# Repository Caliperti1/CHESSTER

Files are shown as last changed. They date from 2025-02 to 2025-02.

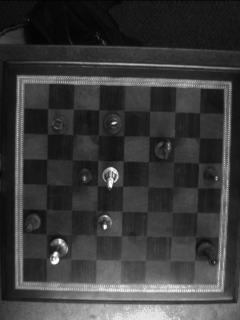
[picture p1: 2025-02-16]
MATLAB/Demo Moved.bmp

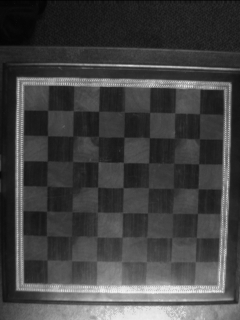
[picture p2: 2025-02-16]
MATLAB/Demo Blank.bmp

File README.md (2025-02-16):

# CHESSTER
Cerebral Harnessing Education Sidekick for STrategic Engineering Research (Chess Robot for Teaching Computer Aided Engineering)

I originally built this project after teaching enginering design, computer aided deisgn, and computational analysis and realzing that students struggled to see how these skills connect to build a cohesive engineering project. 

After using this in class a few students asked to start doing an indepedent study to look into ways of improving the ssytem. Subsequent updates to this repo will be the result of their work!

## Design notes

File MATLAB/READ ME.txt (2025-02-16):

Desktop Chess 
Version 0.1 
Chris Aliperti 
United States Military Academy Department of Civil and Mechanical Engineering 
28 October 2023

--------------------------------------------------------------------------------
Project Overview:

--------------------------------------------------------------------------------
Version Notes:

--------------------------------------------------------------------------------
Arduino Camera:
	This version uses an OV7670 and an arduino on a rig to capture images at 
	every 3 seconds and store them in a folder. 
	Tutorial: https://www.instructables.com/OV7670-Arduino-Camera-Sensor-Module-Framecapture-T/

--------------------------------------------------------------------------------
Solidworks:
	Soldiworks assembly shows camera rig using arduino Uno, OV7670 and 1020 alluminum 

--------------------------------------------------------------------------------
Matlab Functions 

	* denotes unused or archived functions 

	greyScale - normalizes an image to greyscale values (0-1)
		input: image (mxnx3)
		output: normalized image (mxn)

	*BW - turns image to black an dwhite, using mean pixel value as 	threshhold 
		input: image (mxnx3)
		output: BW image with vlaues of 0 or 255 (mxnx3) 

	*squareOffRig - trims image to square matrix with only board using set dimensions based off the camera rig. Archived due to inability to adapt to slight sifts in board or rig.
		input - image (mxnx3)
		output - sqaure image martix where deimasion a is based off difference between provided upper,lower,left adn right ounds of board (axax3) 

	sobelMask - finds edges within an image using a 3x3 mask convoluted over image. Gradient of convolution matrix is calculated and value is compared to a threshold and pulled to rail based on thrshold criteria.
	input - image (nxmx3)
		thresh - value between 0 and 1. hgiher number will make filter more selective 
	output - image of edges (nxm)

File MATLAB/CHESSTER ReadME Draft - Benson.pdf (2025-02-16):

CHESSTER README word doc
play
BLUF: The play function encompasses all of the functions that enable CHESSTER to play with its human opponents through computer vision and an exchange of information between MatLab and Arduino.
- Establishes variables for connection to Arduino serial port. (sets baud rate, loads default camera positions from given files).
- Prompts user in MatLab to recalibrate camera over the chess board
- Reads response and calls calibrateCamera function with the default camera positions as inputs or displays blank image.
- Calls startGame function and sets turn to 0
- Establishes serial connection to Arduino and waits at most 10 minutes before moving to next turn.
- While turn is 0, MatLab communicates to Arduino and displays a standby message. Arduino receives the communication and calls the startPlay function, which changes the standby message on the LCD to a read to play message and send a ready signal back to MatLab.
- MatLab receives start signal and calls the captureImage function, which sets the default image of the chess board, and displays its own ready message while also advancing the turn.
- Arduino receives ready signal from MatLab and prompts the user to begin their move, as well as to press the button on the LCD after their move.
- When the button is pressed, Arduino runs the signalMove function which displays a loading message on the LCD screen and sends a play signal to MatLab.
- When MatLab receives the play signal, it causes the camera to take another image of the board with captureImage, then it runs computer vision by calling the camPassForward function which takes the original image of the board, new image of the board, and startGame functions to run. MatLab then runs the engine for Chesster using the engPassForward function. Moves made are translated and sent to Arduino using json and sent to Arduino.
- Move is received by Arduino, and displays a confirmation message on the LCD, while communicating with MatLab as well.
- Arduino makes a decision based on kill values sent with the move data and displays that the move was received and whether a piece was taken with its move, finally displaying a move complete message (sending another message to MatLab) and prompting the user to make another move and advancing the turn, otherwise an error message will display.
- As MatLab receives confirmation, it displays the acknowledgement and the move made using the showOff function, as well as advancing the turn. When the move complete message is received, MatLab runs the updateGame function and takes another picture of the board using the captureImage function.
- As the player makes another move, the process repeats itself.
Computer Vision

captureImage
BLUF: The captureImage starts the camera and saves images taken to the landing directory, as well as identifying the image for use by other functions later.
Inputs: camDir, landingDir, camKIllBatDir (Directories for starting and stopping the camera, as well as storing the images.
Outputs: Images
- Runs the initiateCamera function with the camera directory as the input.
- Identifies the open directory folder as the original directory, then sets a stat variable as 1.
- While loop that runs when stat = 1, changes open folder to the landing directory folder (where pictures go), sets a search variable “a” to identify any objects in the directory with a .bmp file identifier. Sets variable “n” as the number of objects identified by the “a” variable.
- If statement, that initiates when the number of objects in the landing directory is greater than 9, which in turn runs the kill function to stop the camera from taking photos. If successful, then a script will print stating it executed the kill, otherwise it will display an error message.
- Stat is set to 0, ending the while loop.
- Switches open folder to the landing directory in case it is not, sets the image to the 6th image taken (higher resolution)
- Removes images that it did not identify in the previous step from the landing directory.
- Sets open folder back to the original directory.
initiateCamera
BLUF: Starts camera
Inputs: camDir (Directory that contains the command to start the camera) Outputs: Camera starts
- Sets open folder as the original directory.
- Try (Executes code)
- Sets open folder as the input directory from captureImage.
- Sets the command variable to the code that starts the camera
- Tells Command Prompt to run the start command.
- Sets open folder to the original directory
- Displays a message when command is sent.
- Catch (Catches errors)
- Sets open folder to the original directory
- Displays error message.
calibrateCamera
BLUF: Captures image of blank board and ensures camera is working properly.
Inputs: camDir, landingDir, camKIllBatDir (Directories for starting and stopping the camera, as well as storing the images.
Outputs: Calibrated image of the blank board

- Sets confirmation variable to a default, while default user will be prompted to “press any button when ready to calibrate”
- When a button is pressed, and the ready variable is changed, an if statement is executed, setting the blank image as a variable, that uses the output of the captureImage function.
- squareOffTestFig function is executed with the blank image as the input
- User is prompted to press “Y” to confirm calibration or “N” if a new image needs to be taken. This input replaces the previous confirmation variable.
- A full file specification using the landing directory folder and the 6.bmp image from the folder is set to a current image name variable.
- A second if statement is executed if the user answers the calibration prompt with “Y”.
- A blank.bmp filename is created for the landing directory folder and set as the new image name variable.
- The current image name is changed to the new image name “blank.bmp”
- The blank image variable is reset to the blank.bmp image, and a message is sent confirming the name change.
- All files excluding the newly named .bmp are cleared from the landing directory folder.
squareOffTestFig
BLUF: Takes blank board image, squares it off and makes it greyscale.
Inputs: Initial image of the blank board
Outputs: Calibrated image of the blank board
- Calls sobelMask function, with the blank board image as an input and with a very high threshold in order to outline the entirety of the board.
- Calls the squareOff function with the blank board as the input and isolates the board.
- Displays the three new images in a figure for the user to see.
sobelMask
BLUF: Finds edges and generates an edge map image of the board and squares within. Inputs: Initial blank image of the board, color threshold fo identifying pixels as black or white.
Outputs: Image of the identified white areas on the board.
- Calls greyScale function in input image, normalizing color values between 0 and 1
- Defines the “Mask” matrix to be used in the Sobel.
- Convolutes the mask matrix over the image matrix and returns a convolution matrix, then calculates the magnitude of the convolutions.
- Stores the magnitudes as 1-bit integers as the output of the function.
greyScale
BLUF: Normalizes an image (0 - white, 1 – black) *Figure out numbers in function

Inputs: Initial blank image of the board
Outputs: Grayscale image of the blank board.
- The input image’s colors are reassigned as either black or white depending on which they are closer to in color, and assigned to the output variable. squareOff
BLUF: Square off input image and isolate Board based on calculated bounds.
Inputs: Initial blank image of the board
Outputs: Image of the board after identifying and applying the boundaries of the board in the image.
- Sets the bounds to a variable bound that calls the boardBounds function using the input image to the squareOff function as the same input.
- Sets the x and y bounds of the new squared image as the bounds found in the boards function.
boardBounds
BLUF: ID edges of the board, starting at the center of the sobelmasked image and finds the coordinate of the first edge in each direction with a high threshold, then trims the image to be square.
Inputs: Initial blank image of the board
Outputs: Greyscale image of the board with boundaries applied after identification through use of the Sobel mask.
- Calls the sobelMask function, with the input image and a high threshold.
- Determines the size of the sobelmasked image, then finds the center of it.
- Initiates four while loops that move in each direction until an edge is found
- Coordinates of the edges are put in to a matrix as the output. camPassForward
BLUF: Passes forward the updated game matrix to the engine, using the blank board image, the board image before the move, an image of the board after the move, and a matrix that represents the original image as inputs.
Inputs: Calibrated image of the blank board, an image of the set board before a move, an image of the set board after a move, and the game matrix that represents the board state before a move. Outputs: Updated game matrix that represents the board after a move.
- Calls the findMove function to calculate what on the board has changed.
- Calls the updateGame function to update the game matrix.
findMove
BLUF: Takes blank image of board, the image of the board before the move, and the image of the board after the move and determines what move was made. *Change variables around, check functionality.

Inputs: Calibrated image of the blank board, an image of the board before a move, and an image of the board after a move.
Outputs: Coordinates of the piece before and after it has moved.
- Calls the moveLoc function to find the starting location of the piece and the ending location of the piece, then assigns them to a matrix as the output.
moveLoc
BLUF: Analyzes the input images of the original board and the board with the move made, and determines what move occurred.
Inputs: Calibrated image of the blank board, an image of the board before a move, and an image of the board after a move.
Outputs: Coordinates of the piece being moved in both images and an associated confidence.
- Finds the area in the images where the numerical values in the matrixes differ
- The difference is run through the sobelMask function
- The sobelmasked image is run through the squareOff2 function using the blank board bounds.
- The square bounds of the blank board are then found using the squareOff function, and the sqaureBounds function, which is then assigned as an 8x8 matrix.
- A score is then calculated that gauges the confidence of the move detected by the series of functions.
squareOff2
BLUF: Square off image and isolate Board based on calculated bounds from a blank board
Inputs: Initial blank image of the board, and the Sobel mask of the difference between the images of the board before and after a move.
Outputs: Image of the board after identifying and applying the boundaries of the board in the image.
- Sets the bounds to a variable bound that calls the boardBounds function using the input image to the squareOff function as the same input.
- Sets the x and y bounds of the new squared image as the bounds found in the boardBounds function.
sqaureBounds
BLUF: Creates bounds for the squared image input.
Inputs: Squared image of the blank board
Outputs: Bounds for each square on the chess board.
- Creates dimensional increments of 8 from left to right and top to bottom.
- Creates vectors of these bounds, then corrects them.
- Creates an array that stores the squares in the vicinity of each other.

showOff
BLUF: Plots images of the board before the move and after the move, as well as the results of the computer vision stage.
Inputs: Calibrated image of the blank board, an image of the set board before a move, an image of the set board after a move, and the game matrix that represents the board state before a move. Outputs: Figure that shows side by side images of the board before and after a move, and a digital version of the change the computer vision recognized on the board.
- Calls the findMove function with images of the blank board, board before the move and the board after the move as inputs.
- Assigns the pieces on the board coordinates for both the original board and the moved board using the mapToChess function.
- Calls the updateGame function using the game matrix and the move found.
- Displays a plot of the original board before the move and another of the board after the move, as well as the original and new game matrixes.
mapToChess
BLUF: Converts the matrix coordinates of the board to chess locations.
Inputs: Coordinates of the piece moved in the game matrix
Outputs: Location of the piece on the chess board in corresponding terms
- Assigns the matrix coordinates a chess board position (i.e. knight to a4) displayBoard
BLUF: Creates a figure of the digital representation of the current board give the game matrix. *Does not use the output in the function*
Inputs: The game matrix
Outputs: Figure that represents the current state of the board
- Calls the checkerBoard function and assigns it to a variable.
- Creates a vector of 8 evenly spaced points from 1 to 64 and an 8x8x2 position matrix of zeros.
- Assigns positions to four quadrants of the chess board individually, then compiles them into an image.
checkerBoard
BLUF: Creates a blank checkerboard pattern for plotting.
Inputs: None
Outputs: Blank checkerboard patter to be used to plot a digital representation of the chess board.
- Creates a matrix of ones to represent white, and a matrix of zeros to represent black, and assigns them to an overall matrix for the output.

updateGame
BLUF: Updates the game matrix based on the move made.
Inputs: The current game matrix and the coordinates of a piece before and after a move. Outputs: Updated game matrix for the board after a move has been made.
- Assigns the original position of the piece to x and y variables as well as the new location of the piece.
- Uses the position of the piece and identifies both its type and color using the game matrix as the reference.
- Overwrites the original position of the piece in the game matrix, and sets the new location of the piece in the game matrix.
startGame
BLUF: Creates the game matrix, with pieces at starting locations identified by both color and type. Inputs: None
Outputs: Original game matrix of a set board before any move has been made.
- Assigns a color and piece matrix for the starting board state.
Engine
engPassForward
BLUF: Generates a recommended move and translates it to steps for the motor using the game matrix and turn number as inputs and outputting piece and move locations, as well as info on whether a piece has been taken.
Inputs: Current game matrix and the current turn number.
Outputs: Positions of a piece before and after a move as well as information regarding whether a piece is taken.
- Calls the engine function with the game matrix and turn number as inputs.
- Takes the recommended move and separates it into the coordinates of the piece before and after the move.
- Size parameters are then set for the engine, in reference to the board as well as for the motor’s rotation.
- Sets kill conditions for when one player’s piece overtakes another.
engine
BLUF: Takes in the game matrix and turn, puts them through several layers of a decision tree, returning an array with the information for a recommended move.
Inputs: Current game matrix and the current turn number.

Outputs: A cell array with all relevant information for a recommended move.
- Creates the first layer of the decision tree using the firstLayer function, and a second using the secondLayer function with the first layer as an input.
- Creates a weighted move matrix using the firstLayerOutputWeighted with both layers.
- Attributes a score to the weighted matrix and creates a set of recommended moves. firstLayer
BLUF: Uses the game matrix and turn as inputs, outputting an 8x8 array, where each cell contains the moves the piece in that position can perform. *Nested 8x8 in each part of the output array.*
Inputs: Current game matrix and the current turn number.
Outputs: Cell array with all available moves for the pieces on the board.
- Determines the color of the piece based on the current turn.
- Calls the initFirstLayer function to create an empty move matrix as a shell for the first layer.
- Populates the first layer by running a for loop through the entire game matrix, and assigning moves from the pawnMoves, rookMoves, bishopMoves, knightMoves, queenMoves, and kingMoves based on the piece in each cell.
initFirstLayer
BLUF: Creates the first layer for the engine.
Inputs: None
Outputs: Empty cell array for use in the firstLayer function.
- Assigns the initialization as an 8x8 cell array
- Sets the values of the array as zeros.
secondLayer
BLUF: Creates the second layer of the decision tree for the engine, using the game matrix, turn, and the first layer as inputs.
Inputs: Current game matrix, the current turn number, and the first layer cell array. Outputs: Cell array of all possible moves for the user to make in response to any move possible to CHESSTER in the first layer.
- Determines the color of the piece based on the current turn.
- Calls the movedGame function with the first layer and the game matrix as inputs in order to create an input layer of all possible moved games that can occur as a result of the first layer.
- Calls the initSecondLayer function to create an empty move matrix as a shell for the second layer.
- Populates the second layer by running a for loop through the entire game matrix, and assigning moves from the pawnMoves, rookMoves, bishopMoves, knightMoves, queenMoves, and kingMoves based on the piece in each cell.

movedGame
BLUF: Creates a cell array of all moved games that can occur as a result of first layer moves to be used as inputs for the second layer, uses the first layer and the game matrix as inputs.
Inputs: Current game matrix and the first layer cell array.
Outputs: Cell array of all moved games that can occur as a result of first layer moves.
- Creates an empty cell array and populates it with data from the game matrix and first layer, showing all possible game movements from the game matrix to the first layer.
initSecondLayer
BLUF: Initializes the second layer for the engine using the output from the movedGame function as its input.
Inputs: movedGame cell array
Outputs: An empty input layer cell array.
- Assigns the initialization as an 8x8 cell array
- Sets the values of the array as zeros.
pawnMoves
BLUF: Uses the game matrix, and the position of the piece in the matrix, as inputs to create an 8x8 showing possible moves for pawns.
Inputs: Current game matrix and the coordinates of pawns in the given cell array. Outputs: Coordinates in the cell array of where each pawn could move legally on the board.
- Checks the color of the piece.
- Creates an 8x8 blank matrix for possible moves.
- Assigns if statements for the conditions of the board, to calculate what legal moves can be made for a pawn.
rookMoves
BLUF: Uses the game matrix, and the position of the piece in the matrix, as inputs to create an 8x8 showing possible moves for rooks.
Inputs: Current game matrix and the coordinates of rooks in the given cell array. Outputs: Coordinates in the cell array of where each rook could move legally on the board.
- Checks the color of the piece.
- Creates an 8x8 blank matrix for possible moves.

- Assigns if statements for the conditions of the board, to calculate what legal moves can be made for a rook.
bishopMoves
BLUF: Uses the game matrix, and the position of the piece in the matrix, as inputs to create an 8x8 showing possible moves for bishops.
Inputs: Current game matrix and the coordinates of bishops in the given cell array. Outputs: Coordinates in the cell array of where each bishop could move legally on the board.
- Checks the color of the piece.
- Creates an 8x8 blank matrix for possible moves.
- Assigns if statements for the conditions of the board, to calculate what legal moves can be made for a bishop.
knightMoves
BLUF: Uses the game matrix, and the position of the piece in the matrix, as inputs to create an 8x8 showing possible moves for knights.
Inputs: Current game matrix and the coordinates of knights in the given cell array. Outputs: Coordinates in the cell array of where each knight could move legally on the board.
- Checks the color of the piece.
- Creates an 8x8 blank matrix for possible moves.
- Assigns if statements for the conditions of the board, to calculate what legal moves can be made for a knight.
queenMoves
BLUF: Uses the game matrix, and the position of the piece in the matrix, as inputs to create an 8x8 showing possible moves for queens.
Inputs: Current game matrix and the coordinates of queens in the given cell array. Outputs: Coordinates in the cell array of where each queen could move legally on the board.
- Checks the color of the piece.
- Creates an 8x8 blank matrix for possible moves.
- Assigns if statements for the conditions of the board, to calculate what legal moves can be made for a queen.
kingMoves
BLUF: Uses the game matrix, and the position of the piece in the matrix, as inputs to create an 8x8 showing possible moves for kings.
Inputs: Current game matrix and the coordinates of kings in the given cell array.

Outputs: Coordinates in the cell array of where each king could move legally on the board.
- Checks the color of the piece.
- Creates an 8x8 blank matrix for possible moves.
- Assigns if statements for the conditions of the board, to calculate what legal moves can be made for a king.
firstLayerOutputWeighted
BLUF: Uses the game matrix, first layer, second layer, and turn number as inputs to weigh the decisions in the first and second layer, takes the difference, and applies the move to a “dictionary” where the overall maximum difference is chosen as the best move.
Inputs: Current game matrix, the first layer cell array, second layer cell array, and the current turn number.
Outputs: Score key associated with every possible move on the board.
- Determines the color of the piece based on the turn.
- Creates a weight dictionary for the value of each piece.
firstLayerOutput
BLUF: Checks the second layer and determines whether the move would result in the opponent being able to take CHESSTER’s king.
Inputs: Current game matrix, the first layer cell array, second layer cell array, and the current turn number.
Outputs: Weight of every move in the first layer cell array.
- Creates a cell array with all of the information about possible moves and their attributed score.
- Determines the location of the friendly king on the board.
- Creates an empty matrix the size of the second layer.
- Analyzes the moves available to CHESSTER using the listMoves function.
- Uses the second layer to determine which of the moves in the move list leave the opportunity for the user to take CHESSTER’s king.
- Determines if the move made by CHESSTER would be legal or would result in the loss of its king.
- Outputs a cell array with all relevant information pertaining to moves that could be made including piece identifying information, locations, scores related to moves, and the enemy’s best response.
listMoves
BLUF: Lists all moves available to CHESSTER from the first layer Inputs: Current game matrix and the first layer cell array. Outputs: List of all moves available from the first layer.
- Creates an empty string array

- Populates the array with information from the first layer, using the location from the first layer as it relates to the game matrix and calling the mapToChessPlot function to convert the game matrix coordinates to locations on the chess board.
mapToChessPlot
BLUF: Converts game matrix coordinates to chess locations. Inputs: Game matrix coordinates
Outputs: Corresponding chess board locations secondLayerOutput
BLUF: Translates the output of the second layer into a 7-cell array format. Inputs: Current game matrix and the second layer cell array.
Outputs: 7-cell array identifying each piece and its possible moves in response to the first layer
- For every possible move found in the second layer, it is assigned as part of the output array that identifies it by piece type, color, locations, score, and corresponding first layer move.

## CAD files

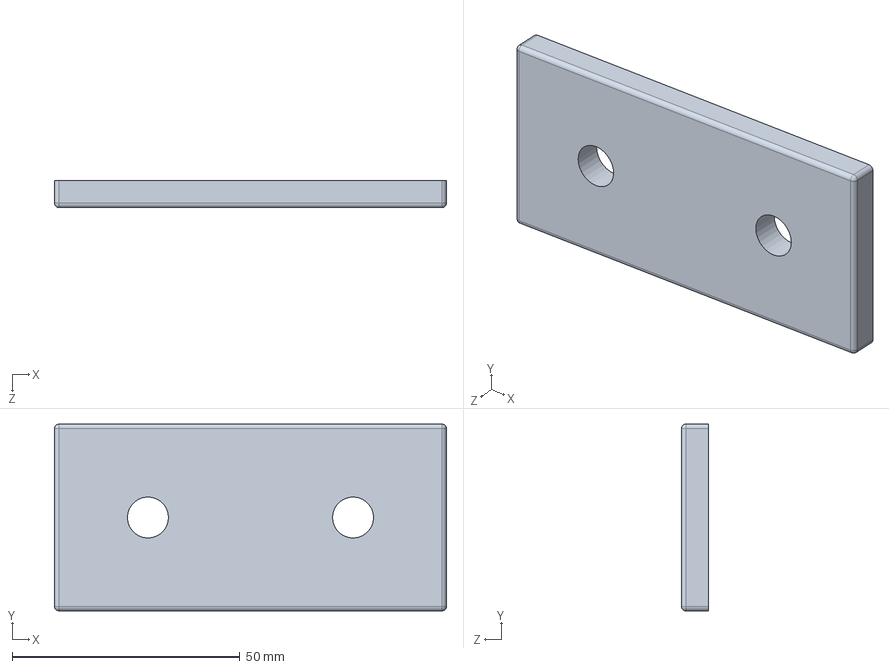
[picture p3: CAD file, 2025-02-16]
Solidworks/Straight connector.SLDPRT
86.0 x 41.0 x 6.00 mm

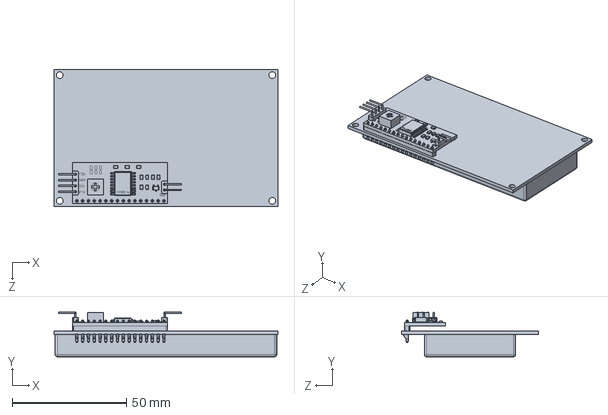
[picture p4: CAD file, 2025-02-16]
Solidworks/lcd 2004 i2c v1.SLDPRT
98.0 x 19.6 x 60.0 mm

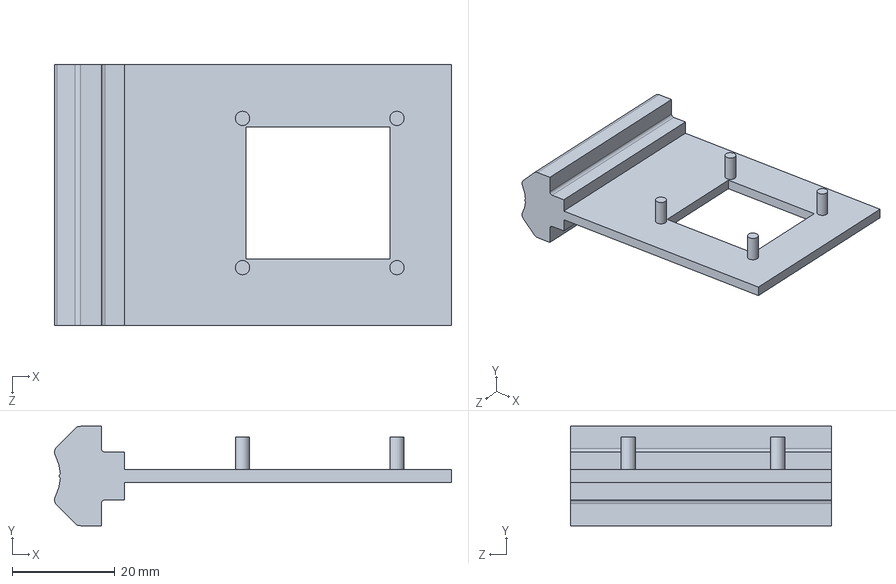
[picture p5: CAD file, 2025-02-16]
Solidworks/OV760 Camera Mount 10mm 8020.SLDPRT
77.1 x 19.3 x 50.8 mm

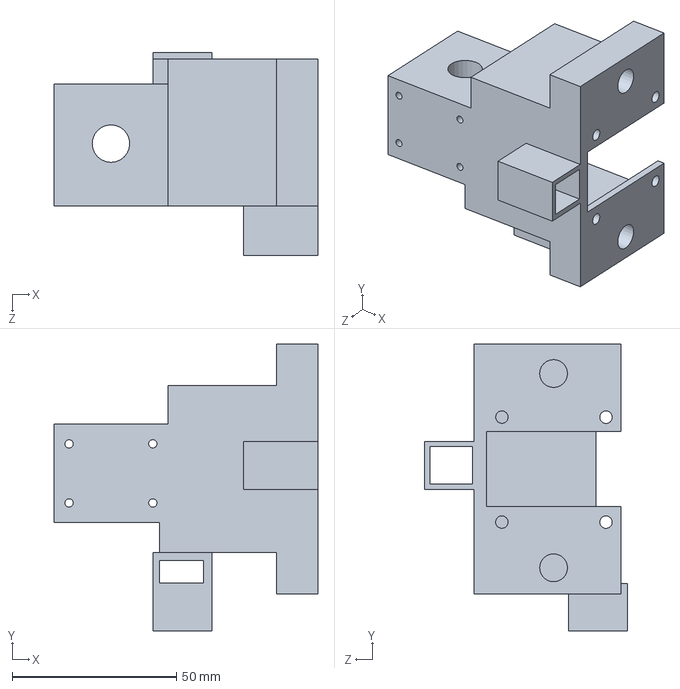
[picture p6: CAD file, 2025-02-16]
Solidworks/Motor Slider.SLDPRT
80.4 x 87.4 x 61.8 mm

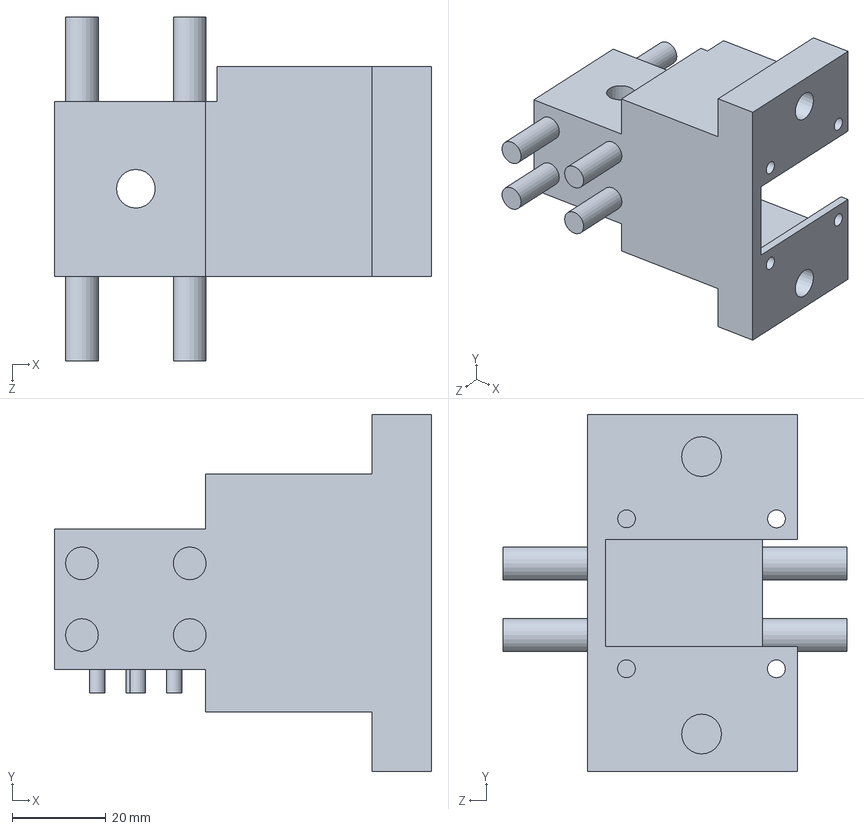
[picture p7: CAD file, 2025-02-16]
Solidworks/Motor Slider-DESKTOP-MGNFT40.SLDPRT
80.4 x 76.2 x 73.3 mm

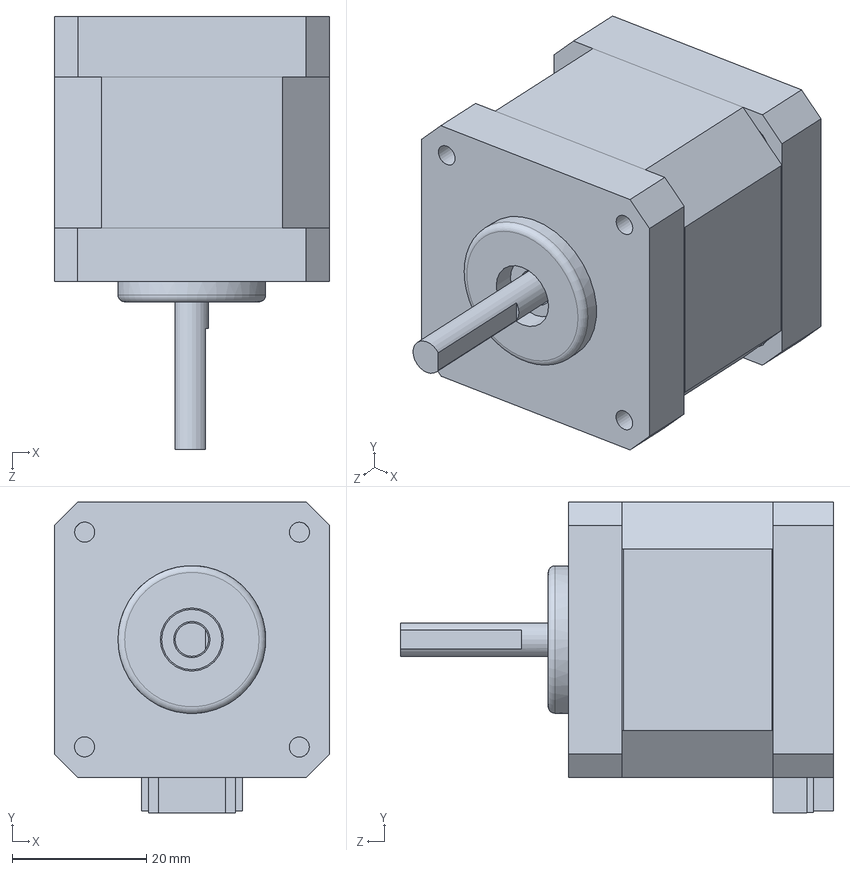
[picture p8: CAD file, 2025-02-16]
Solidworks/Nema 17 Stepper Motor v5.SLDPRT
41.0 x 46.3 x 64.5 mm

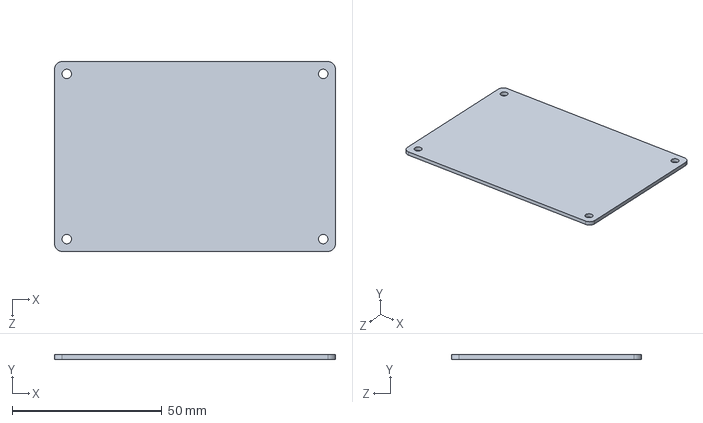
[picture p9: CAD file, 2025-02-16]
Solidworks/protoBoard.SLDPRT
94.0 x 1.52 x 63.5 mm

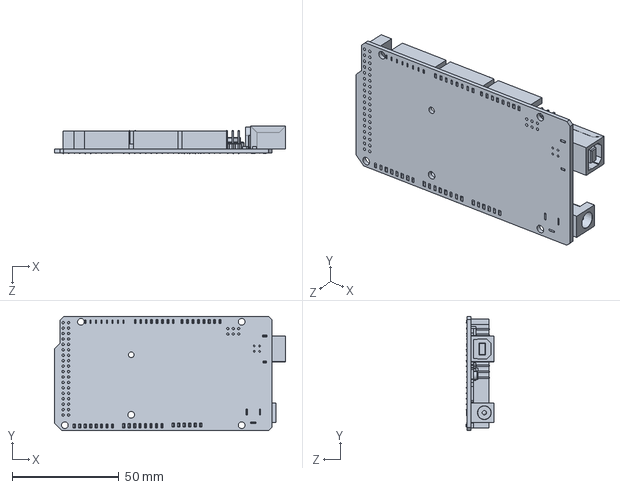
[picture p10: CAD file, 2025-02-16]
Solidworks/ArduinoMega.SLDPRT
107.9 x 53.4 x 13.0 mm

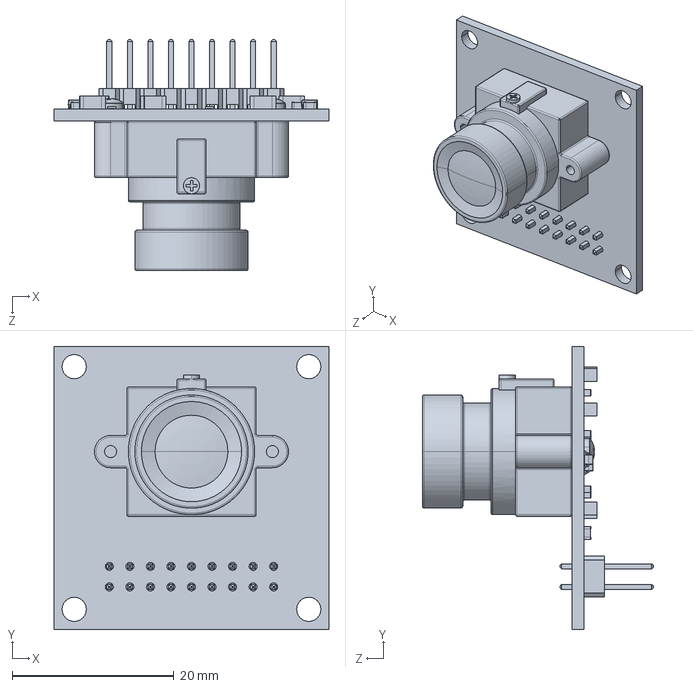
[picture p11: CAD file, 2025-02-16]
Solidworks/Camera OV7670.SLDPRT
34.0 x 35.0 x 28.6 mm

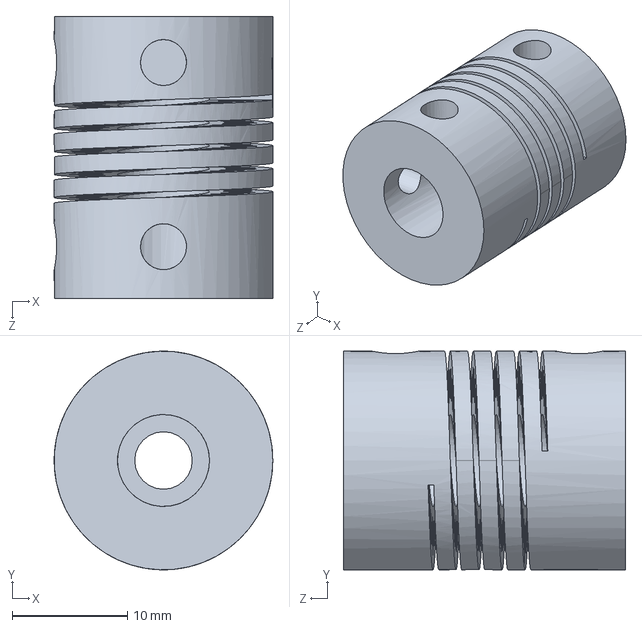
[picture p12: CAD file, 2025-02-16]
Solidworks/Coupler 5mm to 8mm.SLDPRT
19.0 x 19.0 x 24.5 mm

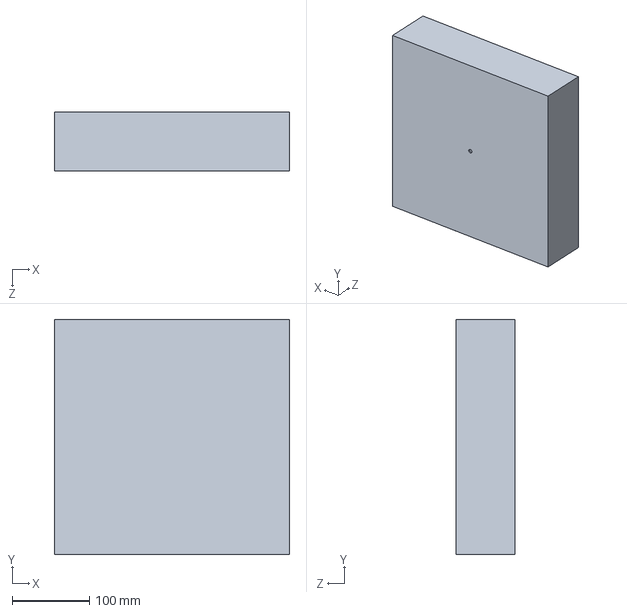
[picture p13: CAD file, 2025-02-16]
Solidworks/Board.SLDPRT
304.8 x 304.8 x 76.2 mm

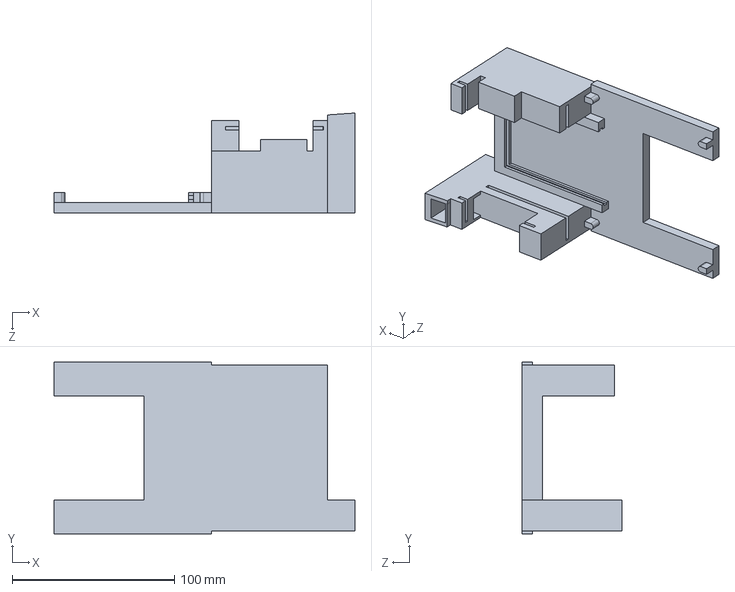
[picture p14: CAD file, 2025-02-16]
Solidworks/ConrtolBox.SLDPRT
185.6 x 106.0 x 61.7 mm

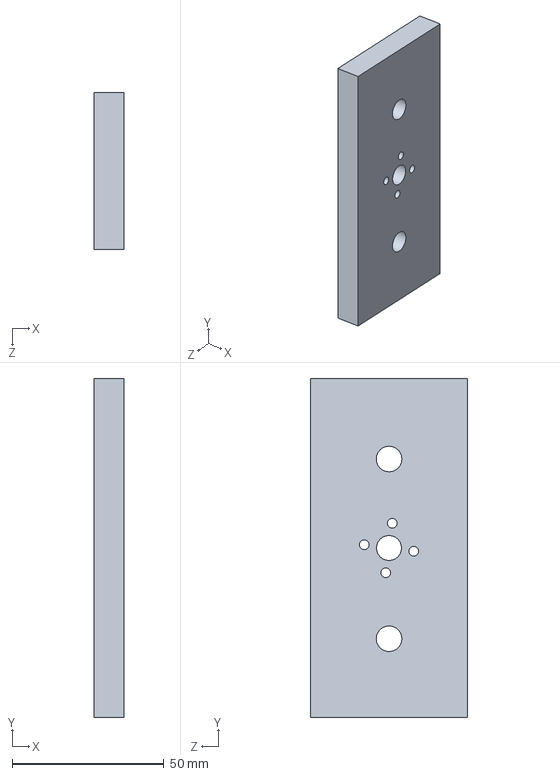
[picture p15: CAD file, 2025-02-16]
Solidworks/Grabber Slider.SLDPRT
10.0 x 111.6 x 51.7 mm

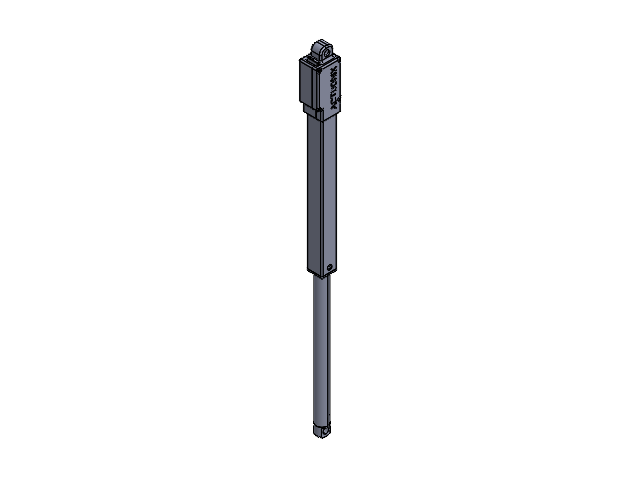
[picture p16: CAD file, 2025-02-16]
Solidworks/l12_100mm_out.SLDASM
EXTENSION_10405_100MM.stp
CLAMSHELL_BOT_10417.stp
CLAMSHELL_TOP_10416.stp
FASTENER_10427.stp x 4
GUIDE_10429.stp
NUT_10419.stp
SHAFT_10410_100MM.stp
PLUG_10428.stp
GROMMET_3_HOLE.stp

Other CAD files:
Solidworks/x axis support.SLDPRT
Solidworks/Part2.SLDPRT
Solidworks/guide rod.SLDPRT
Solidworks/End piece.SLDPRT
Solidworks/1 Inch 80-20 4 Slot.SLDPRT
Solidworks/10mm T slot 8020.SLDPRT
Solidworks/12v_connector_female_.SLDPRT
Solidworks/12v_connector_female_.stp
Solidworks/12v_connector_male_.stp
Solidworks/18in 8020 2.SLDPRT
Solidworks/18in 8020.SLDPRT
Solidworks/2ft 8020.SLDPRT
Solidworks/2in.SLDPRT
Solidworks/3in 8020.SLDPRT
Solidworks/45 deg brace.SLDPRT
Solidworks/47065T602_T-Slotted Framing.SLDPRT
Solidworks/8020 corner mount.SLDPRT
Solidworks/8mm flanged lead screw nut with 2mm thread.SLDPRT
Solidworks/8mm linear bearing with pillow block-8mm linear bearing with pillow block.stp1.SLDPRT
Solidworks/8mm linear bearing with pillow block.SLDPRT
Solidworks/Arduin Uno 8020 Mount.SLDPRT
Solidworks/Camera Mount.SLDPRT
Solidworks/Copy of bracket stepper to 8020-DESKTOP-MGNFT40.SLDPRT
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

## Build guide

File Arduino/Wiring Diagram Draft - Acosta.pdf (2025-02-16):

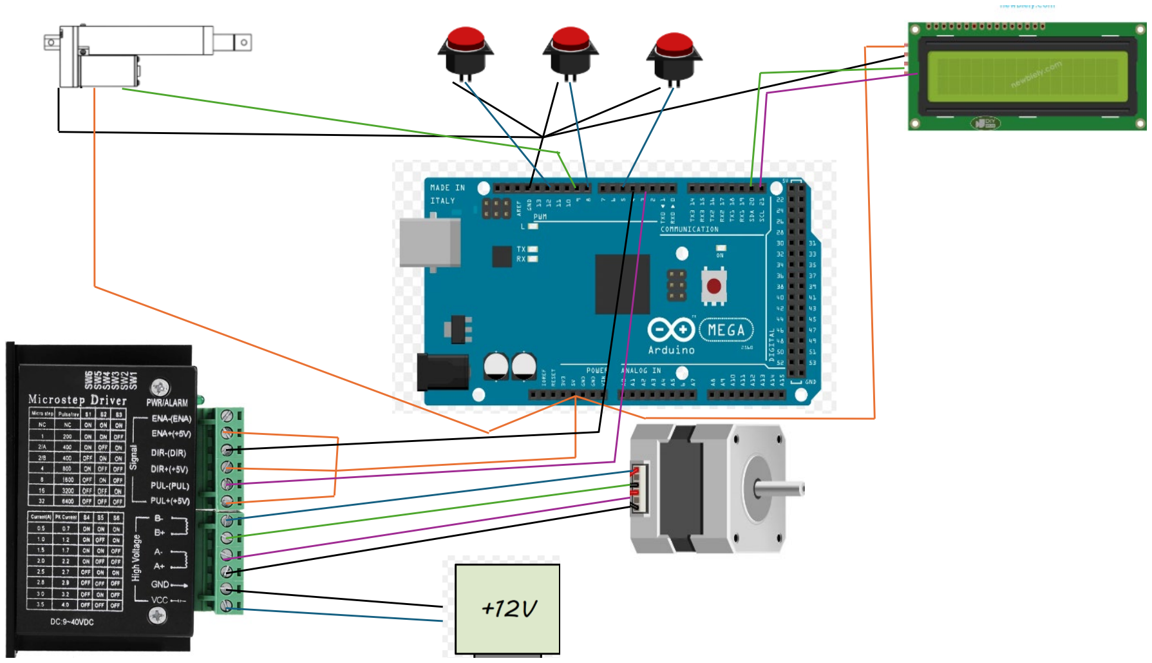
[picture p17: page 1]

## Homing Buttons

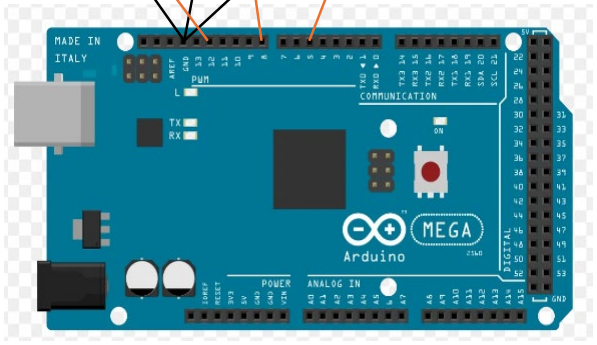
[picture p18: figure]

- Each button has a wire that connects to ground, as well as a button that connects to an individual digital pin
- The X-homing pin is connected to the number “5” pin slot
- It allows for the homing of the X-direction motor
- The Y-homing pin is connected to the number “8” pin slot
- It allows for the homing of the Y-direction motor
- The “Turn” button is connected to the number “12” pin slot
- It is the reset button for the algorithm, and allows for the player to interact with the machine to tell it that the player has completed their turn
- Once pressed, the program will analyze the move, and react accordingly

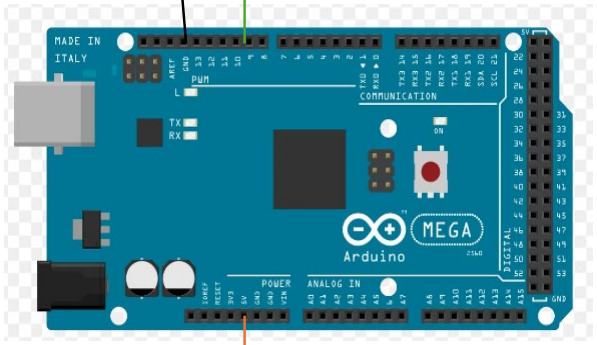
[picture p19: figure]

## The Linear Actuator

- The Linear Actuator has 3 different pin connections
- It has a ground (GND) connection, a power (5V) connection, and digital pin connection
- The digital pin wire is connected to pin slot number “9”
- This pin connection allows for the use of the servo function to be called and recognized by the code
- Additionally, it allows for us to run different functions and transmit that back to the Arduino and actuator

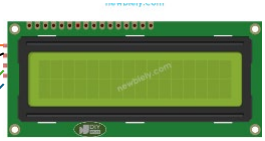
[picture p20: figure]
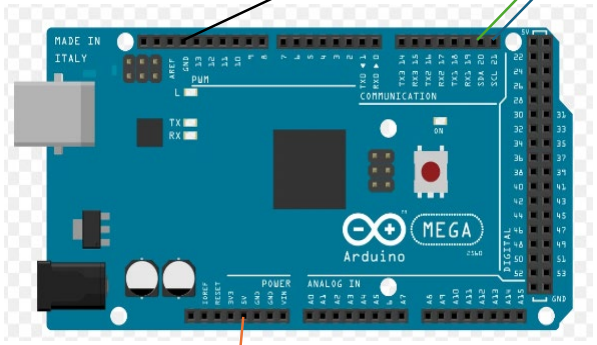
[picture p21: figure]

## LCD Display

- The LCD display is used to show the action that the program is running
- For example, the display reads, “On Standby” when the robot turns on and is waiting for a turn
- The LCD has 4 pins that it is connected to: GND (Ground), 5V (for power), SCL (Serial Clock, which synchronizes data in or out of the target device), and SDA (Serial Data, which transmits data between devices)
- The LCD Display is called using an “include” function, and a representation function that defines the screen size
- The function “lcd.init()” initiates the screen, “lcd.backlight()” turns on the screen, “lcd.setCursor(1,0)” sets the cursor position at the first box, “lcd.print()” allows for certain messages to be displayed by the screen and are typed directly into the function through the parentheses in quotations

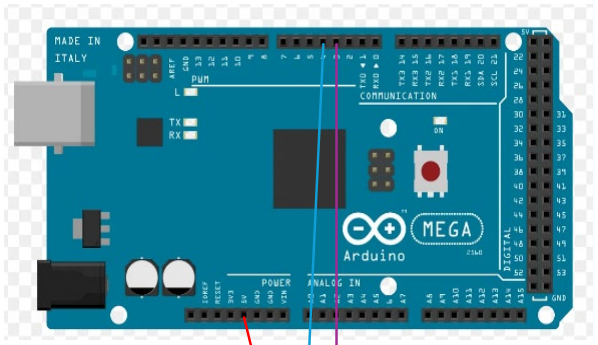
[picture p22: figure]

## The Stepper Motor, Microstep Driver, and External Power Supply (2X):

- The stepper motor and 12V power supply are both routed to the driver which is then routed to the board through the 5V (Power), and two pin connections: one which controls the direction (in this diagram it is represented by the 4-pin), and the other which controls the step (represented by the 3-pin)
- The direction pin control the direction that the motor will travel, with two motors (the other is not displayed for simplicity), one driver/motor combo controls x-direction movement while the other control y-direction movement
- To set up a motor we define it using the “define” function and then we set both the direction and step to different pins
- Next, we declare the pins by calling them as outputs using the “pinMode()” command
- To use the motors, we utilize the “movex()” or “movey()” commands depending on the direction we want to travel
- After the machine has finished its “turn” we can utilize the “homex()” and “homey()” commands, in which case, the motors will spin until the home button is depressed, signifying that the machine has finished its turn

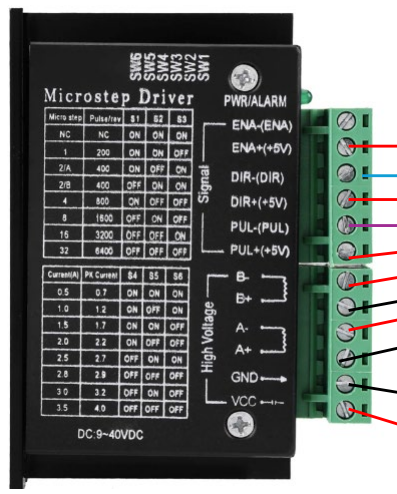
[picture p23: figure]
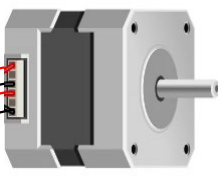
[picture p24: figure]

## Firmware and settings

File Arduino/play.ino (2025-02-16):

// Chesster main control loop 

////////////// Pinout ////////////// 
// X axis home button pin- 5
// X axis driver step pin - 3
// X axis driver direction pin - 4
// Y axis home button pin- 8
// Y axis driver step pin - 6
// Y axis driver direction pin - 7
// Linear Actuator servo pin - 9
// Play button pin - 12
// LCD SDA - 20
// LCD SCL - 21


// Include relevant libraries 
#include <ArduinoJson.h>
#include <LiquidCrystal_I2C.h>
#include <Servo.h>
#include <avr/wdt.h>

//Instantiate Display 
LiquidCrystal_I2C lcd(0x27, 20, 4);

 // initialize stepper pins and actuator 
  #define dirPinx 4 
  #define stepPinx 3
  #define dirPiny 7 
  #define stepPiny 6
  #define servoPin 9

  // define button pins
  #define xhomePin 5
  #define yhomePin 8
  #define turnBut 12

  // define buffer size 
  #define SERIAL_BUFFER_SIZE 512
  
  // Instanitate Linear servo
  Servo linearServo;

  // initialize variables 
  int xorig = 0;
  int yorig = 0;
  int xnew = 0;
  int ynew = 0;
  bool kill = 0;

  int turn = 0;

void setup() {

  // Declare pins as Outputs
	pinMode(stepPinx, OUTPUT);
	pinMode(dirPinx, OUTPUT);

  pinMode(stepPiny, OUTPUT);
	pinMode(dirPiny, OUTPUT);

  pinMode(servoPin,OUTPUT);

  // Declare Homing pins 
  pinMode(xhomePin, INPUT_PULLUP);
  pinMode(yhomePin, INPUT_PULLUP);
  pinMode(turnBut, INPUT_PULLUP);


  // Attach servo pin
  linearServo.attach(servoPin);

  // Initialize LCD
  lcd.init();
  lcd.backlight();
  lcd.setCursor(1, 0);
  lcd.print("ARDUINO STANDING BY");

  // initialize serial connection
  Serial.begin(9600);

}

void loop() {

  int buttonState = digitalRead(turnBut);

  // Standby for serial transmission from matlab 
  if (buttonState == LOW) {
  // Button is pressed (transition from HIGH to LOW)
    if (turn == 0) 
    {
      startPlay();
      turn += 1;
      lcd.setCursor(18,3);
      lcd.print(turn);
      delay(1000);
    } 
    else {
      signalMove();
      turn += 1;
      lcd.setCursor(18,3);
      lcd.print(turn);
      delay(1000);
    }
  }


 if (Serial.available() > 0) {

    String incomingData = "";
    incomingData = Serial.readStringUntil('\n');
    delay(100);
    lcd.setCursor(1, 1);
    lcd.print(incomingData);

    // Check for a trigger signaling move data is incoming at the beginning of the string
    if (incomingData.startsWith("** MOVE:")) {
      updateFromJson(incomingData, xorig, yorig, xnew, ynew, kill);

      lcd.clear();
      lcd.setCursor(1, 0);
      lcd.print("Move Received");
      delay(1000);

      String response = "** Arduino Received Move \n";
      Serial.print(response);

      if ( kill == 1){
        lcd.clear();
        lcd.setCursor(1, 0);
        lcd.print("Move Received - kill");
        delay(1000);
        killMove();
      }
      else if ( kill == 0){
        lcd.clear();
        lcd.setCursor(1, 0);
        lcd.print("Move Received - No kill");
        delay(1000);
        emptyMove();
      }
      else {
        lcd.clear();
        lcd.setCursor(1, 0);
        lcd.print("ERROR W/ KILL LOGIC");
        Serial.print("** ERROR W/ KILL LOGIC");
      }
      lcd.clear();
      lcd.setCursor(1, 0);
      lcd.print("Move Complete");
      Serial.print("** MOVED\n");

      lcd.setCursor(1, 1);
      lcd.print("Your Move");
   
       turn += 1;
    }
  }
}
// Move x poisiton motor
void movex(int steps){
  // spin stepper clockwise 
  digitalWrite(dirPinx, HIGH);

  lcd.clear();
  lcd.setCursor(1, 0);
  lcd.print("Moving X");
  lcd.setCursor(1, 1);
  lcd.print(steps);

  for(int x = 0; x < steps; x++)
	{
		digitalWrite(stepPinx, HIGH);
		delay(10);
		digitalWrite(stepPinx, LOW);
		delay(10);
	}
}

// Move y poisiton motor 
void movey(int steps){
  // spin stepper clockwise 
  digitalWrite(dirPiny, HIGH);

  lcd.clear();
  lcd.setCursor(1, 0);
  lcd.print("Moving Y");
  lcd.setCursor(1, 1);
  lcd.print(steps);

  for(int y = 0; y < steps; y++)
	{
		digitalWrite(stepPiny, HIGH);
		delay(10);
		digitalWrite(stepPiny, LOW);
		delay(10);
	}
}

//Lower linear actuator
void extendz(){
  lcd.clear();
  lcd.setCursor(1, 0);
  lcd.print("Extending Z");

  linearServo.writeMicroseconds(2000);
  delay(5000);
}

//Raise linear actuator
void retractz(){
  lcd.clear();
  lcd.setCursor(1, 0);
  lcd.print("Retracting Z");
  linearServo.writeMicroseconds(1000);
  delay(5000);
}

// home x stepper 
void homex(){

  lcd.clear();
  lcd.setCursor(1, 0);
  lcd.print("Homing X");

  while (digitalRead(xhomePin)) {    
    digitalWrite(dirPinx, LOW);    
    digitalWrite(stepPinx, HIGH);
    delay(10);                       
    digitalWrite(stepPinx, LOW);
    delay(10);   
  }
  while (!digitalRead(xhomePin)) { 
    digitalWrite(dirPinx, HIGH); 
    digitalWrite(stepPinx, HIGH);
    delay(10);                      
    digitalWrite(stepPinx, LOW);
    delay(10);
  }
  lcd.clear();
  lcd.setCursor(1, 0);
  lcd.print("Homing X - Complete");
}

// home y stepper 
void homey(){

  lcd.clear();
  lcd.setCursor(1, 0);
  lcd.print("Homing Y");

  while (digitalRead(yhomePin)) {    
    digitalWrite(dirPiny, LOW);    
    digitalWrite(stepPiny, HIGH);
    delay(10);                       
    digitalWrite(stepPiny, LOW);
    delay(10);   
  }
  while (!digitalRead(yhomePin)) { 
    digitalWrite(dirPiny, HIGH); 
    digitalWrite(stepPiny, HIGH);
    delay(10);                      
    digitalWrite(stepPiny, LOW);
    delay(10);
  }
  lcd.clear();
  lcd.setCursor(1, 0);
  lcd.print("Homing Y - Complete");
}

// home all motors 
void home(){
  homex();
  delay(1500);
  homey();
  delay(1500);
}

// Move to empty space 
void emptyMove(){

  // Move motors to current location of piece 
  movex(xorig);
  movey(yorig);
  delay(1000);

  // grab piece 
  extendz();
  delay(1000);
  retractz();

  // Move motors to new locations 
  movex(xnew);
  movey(ynew);

  // Release piece 
  extendz();
  delay(1000);
  retractz();

  // home motors 
  home();
}

// Move to occupied space
void killMove(){

  int xgrave = 100; // CHANGE TO ACTUAL VALUE 
  int ygrave = 100; // CHANGE TO ACTUAL VALUE 

  // Move motors to currently occupied new space 
  movex(xnew);
  movey(ynew);
  delay(1000);

  // grab piece 
  extendz();
  delay(1000);
  retractz();

  // Move motors to graveyard
  movex(xgrave);
  movey(ygrave);
  delay(1000);

  // Release piece 
  extendz();
  delay(1000);
  retractz();

  // home motors 
  home();

  // Move motors to current location of piece 
  movex(xorig);
  movey(yorig);
  delay(1000);

  // grab piece 
  extendz();
  delay(1000);
  retractz();

  // Move motors to new locations 
  movex(xnew);
  movey(ynew);
  delay(1000);

  // Release piece 
  extendz();
  delay(1000);
  retractz();

  // home motors 
  home();
}

void updateFromJson(const String& incomingData, int &xorig, int &yorig, int &xnew, int &ynew, bool &kill) {

  // Extract the JSON string after the start command
  String jsonStr = incomingData.substring(8); // Skip "** MOVE: "

  // Parse the JSON string
  StaticJsonDocument<512> doc;
  DeserializationError error = deserializeJson(doc, jsonStr);

  // Check for parsing errors
  if (error) {
    Serial.print("** Error parsing JSON: ");
    Serial.println(jsonStr);
    return;
  }

  // Update the function parameters with the JSON values
  xorig = doc["xo"];
  yorig = doc["yo"];
  xnew = doc["xn"];
  ynew = doc["yn"];
  kill = doc["kill"];

}

void startPlay(){

    lcd.clear();
    lcd.setCursor(1, 0);
    lcd.print("GETTING READY TO PLAY");

    home();
    lcd.clear();
    lcd.setCursor(1, 0);
    String mess = "** ARDUINO READY \n";
    lcd.print(mess);
    Serial.print(mess);

  // Matlab will send ready signal back 
    String incomingData = Serial.readStringUntil('\n');
    lcd.clear();
    lcd.setCursor(1, 0);
    lcd.print(incomingData);

    if (incomingData.startsWith("MATLAB READY")){
      lcd.clear();
      lcd.setCursor(1, 0);
      lcd.print("YOUR MOVE");
      lcd.setCursor(1, 1);
      lcd.print("PRESS BUTTON AFTER MOVE");
  } 
}

void signalMove() {
    lcd.clear();
    lcd.setCursor(1, 0);
    lcd.print("...Thinking...");
    Serial.print("** PLAY \n");
}

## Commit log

2025-02-16 Create CAD folder
2025-02-16 Create Arduino Folder
2025-02-16 Uploading Geo's wiring diagram
    Draft of wiring diagram made by Geo during his independent study
2025-02-16 Uploading CHESSTER Assembly file
2025-02-16 CHESSTER Assembly file
2025-02-16 First batch of CAD files
    [1 Inch 80-20 4 Slot.SLDPRT, 10mm T slot 8020.SLDPRT, 12v_connector_female_.SLDPRT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]
2025-02-16 Second batch of CAD files
    [ArduinoMega.SLDPRT, Board.SLDPRT, Camera Mount.SLDPRT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]
2025-02-16 Uploading third batch of CAD files
    [Motor Slider-DESKTOP-MGNFT40.SLDPRT, Motor Slider.SLDPRT, Nema 17 Stepper Motor v5.SLDPRT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]
